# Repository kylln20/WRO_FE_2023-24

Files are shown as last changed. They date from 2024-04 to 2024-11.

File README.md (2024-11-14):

&nbsp;

🛠️ Engineering Documentation 🛠️
======

> This repository details Team Asparagus’ building and programming process in our second participating year of the 2024 WRO Future Engineers Competition.
&nbsp; 

---

## Content of Repository 
* `models` - 3D CAD files
* `others` - Other essential files
* `schemes` - Electrical schematics
* `src` - Main and other programs to run/control software
* `t-photos` - Team photos
* `v-photos` - Robot photos
* `video` - Video demonstration
&nbsp; 

Team Members
---

* Kayla Lin, 17, kylln2027@gmail.com
* Eric Rao, 16, ericrao08@gmail.com
* Brian Yin, 17, brianyin256@gmail.com

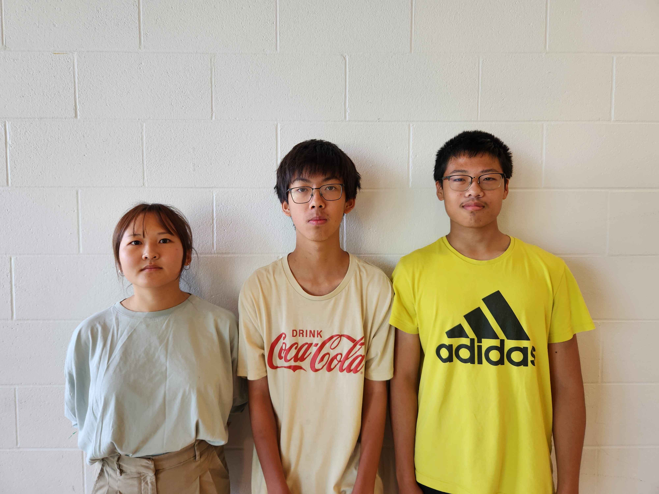
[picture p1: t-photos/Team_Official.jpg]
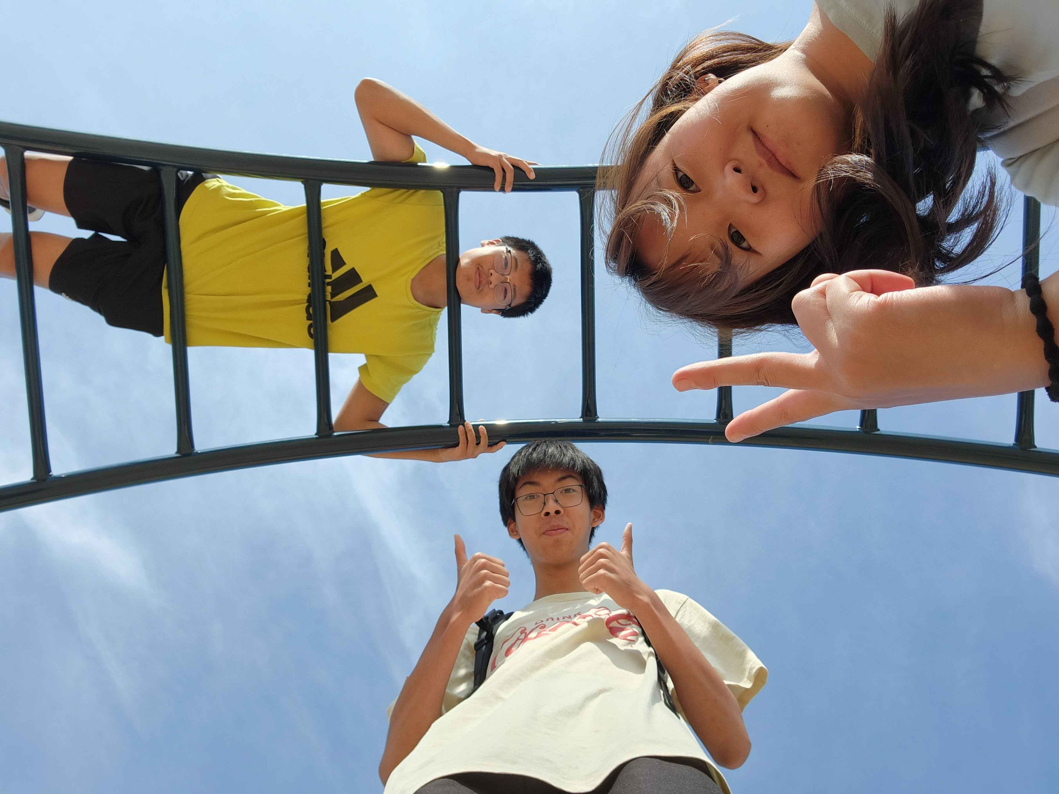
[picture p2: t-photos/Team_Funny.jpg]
 

***Kayla Lin (Left), Eric Rao (Middle), Brian Yin (Right)***

## 📖 Content of README 📖
* **[Hardware](#-hardware-)**
  * [Components](#%EF%B8%8F-components-%EF%B8%8F)
  * [Mobility Management](#-mobility-management-)
    * [Chassis](#chassis)
    * [Design](#design)
    * [Motors](#motors)
  * [Power and Sense Management](#-power-and-sense-management-)
    * [Power and Wiring](#power-and-wiring)
    * [Sensors](#sensors)
    * [Schematic](#schematic)
* **[Software](#-software-)**
  * [Initialization and Connection Process](#-initialization-and-connection-process-)
  * [Object Management](#object-management)
    *  [Object Detection](#object-detection--open-challenge--obstacle-challenge-)
    *  [Wall Detection/Management](#wall-detectionmanagement--open-challenge--obstacle-challenge-)
    *  [Signal Pillar Detection/Management](#signal-pillar-detectionmanagement--obstacle-challenge-)
    *  [Turning (Open Challenge)](#turning--open-challenge-)
    *  [Turning (Obstacle Challenge)](#turning--obstacle-challenge-)
    *  [Parking Lot Detection/Management](#parking-lot-detectionmanagement--obstacle-challenge-)
    *  [Three-Point Turn](#three-point-turn--obstacle-challenge-)
    *  [Backing Up](#backing-up--obstacle-challenge-)
    *  [Potential Improvement: Stuck Detection](#potential-improvement-stuck-detection--open-challenge--obstacle-challenge-)
* **[Assembly Instructions](#-complete-assembly-instructions-)**
  
&nbsp;

---

&nbsp;

🤖 Hardware 🤖
===

### ⚙️ Components ⚙️

| Name | Product | Price |
| --- | --- | --- |
| RC Car | [`Carisma GT24`](https://www.canadahobbies.ca/product/hobby-brands/carisma-rc/gt24-124th-4wd-toyota-celica-gt-four-st185-wrc/) | $263 |
| RC Car Battery | [`Gens Ace 1300mAh Battery`](https://www.adrenalinehobby.com/products/gens-ace-g-tech-1300mah-2s-7-4v-25c-lipo-deans-plug) | $35 | 
| Drive Motor & ESC | [`Furitek Komodo Motor + Lizard Pro ESC`](https://www.xtremerc.ca/products/furitek-scx24-stinger-brushless-power-system-w-1212-3450kv-brushless-motor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) | $226 |
| Turning Motor | [`Hitec HS-5055MG Servo Motor`](https://ca.robotshop.com/products/hs-5055mg-metal-gear-micro-servo-motor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) | $38 |
| Motor Mount | [`GT24 High Performance Alloy Motor Mount`](https://carisma-shop.com/products/gt24-alum-motor-mount) | $17 |
| CSI Camera | [`SainSmart Wide Angle Fish-Eye Camera`](https://www.amazon.ca/SainSmart-Fish-Eye-Camera-Raspberry-Arduino/dp/B00N1YJKFS/ref=sr_1_5) | $19 |
| Raspberry Pi HAT | [`HiWonder TurboPi HAT`](https://www.hiwonder.com/collections/raspberrypi-bionic-robot/products/turbopi?variant=40112905388119) | $61 [^1] |
| Raspberry Pi | [`Vemico Raspberry Pi 4`](https://www.amazon.ca/Vemico-Raspberry-Kit-Heatsinks-Screwdriver/dp/B09WXRCYL4/ref=sr_1_3) | $176 |
| Raspberry Pi Fan | [`GeeekPi Fan`](https://www.amazon.ca/dp/B07C9H9LJN?psc=1&ref=ppx_yo2ov_dt_b_product_details) | $19 |
| ON OFF Switch | [`DaierTek Switch`](https://a.co/d/05vnrpJD) | $13 |

**Total Car Cost: $867 CAD**

[^1]: This link is for the `Hiwonder TurboPi Car`, which uses the `HiWonder TurboPi HAT`. We contacted the manufacturer to purchase the HAT directly.

<sup>*3D printed parts were made with the [`BambuLab P1P`](https://ca.store.bambulab.com/products/p1p)</sup>

&nbsp;

🚗 Mobility Management 🚗
---

### Chassis
We use the chassis of the `Carisma GT24`, a pre-built 1/24 scale RC car (15 cm in length) to accommodate the added challenge of the magenta parking lot in the obstacle challenge. It allows us to park head-on, as opposed to parallel parking. Head-in parking has fewer steps, reducing our obstacle challenge time. Also, while head-in parking, the car only needs to be aware of what is beside it and what is in front of it, which can be assessed with a single front-facing camera. Comparatively, to perform parallel parking, a car will usually need to reverse, requiring an additional rear-facing sensor. Such would unnecessarily complicate the system.

The chassis also enables a four-wheel drive system, with pre-integrated gearboxes. This system offers benefits over a two-wheel drive system increasing the car's traction, stability, and acceleration due to the power distribution between four wheels instead of two. 

#### Potential Chassis Improvement
Although the chassis has many benefits, its design only allows a maximum turning angle of 50 degrees. Although sufficient for our task, a car with a chassis with a greater turning angle would more easily navigate the challenges and could be pushed to navigate at a higher speed. Swapping the chassis for one with a higher turning angle, whether store-bought or 3D-printed, would significantly improve the car's movement and obstacle avoidance. We have also seen that one can modify the original chassis to have a much greater turning angle, but we decided against it due to time constraints. 

This is a video example of a modification done to a similar chassis: 

[K989 Modification](https://www.youtube.com/watch?v=JmsCxSgEJnU)

### Design 

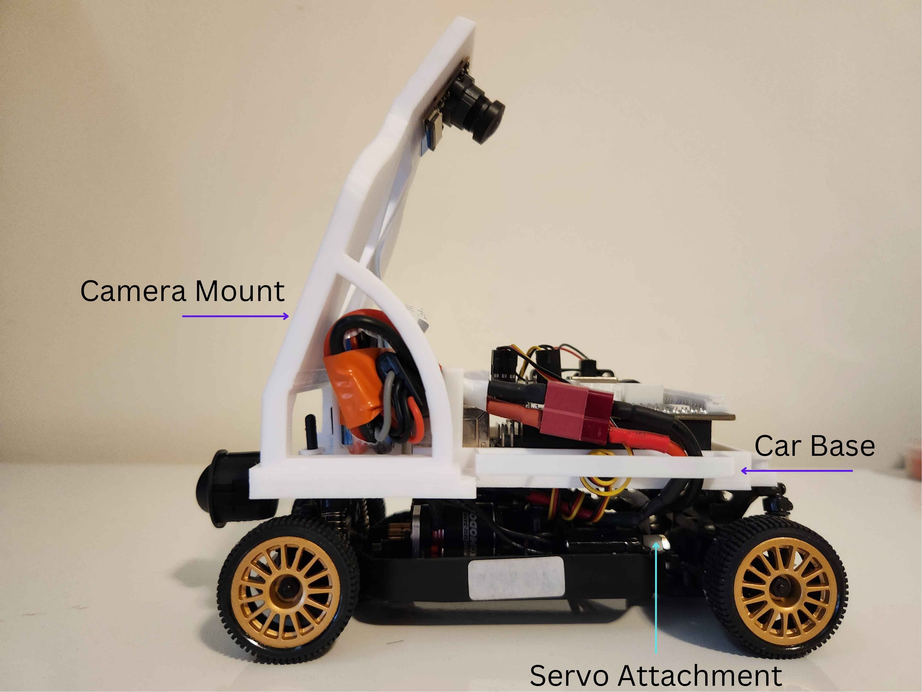
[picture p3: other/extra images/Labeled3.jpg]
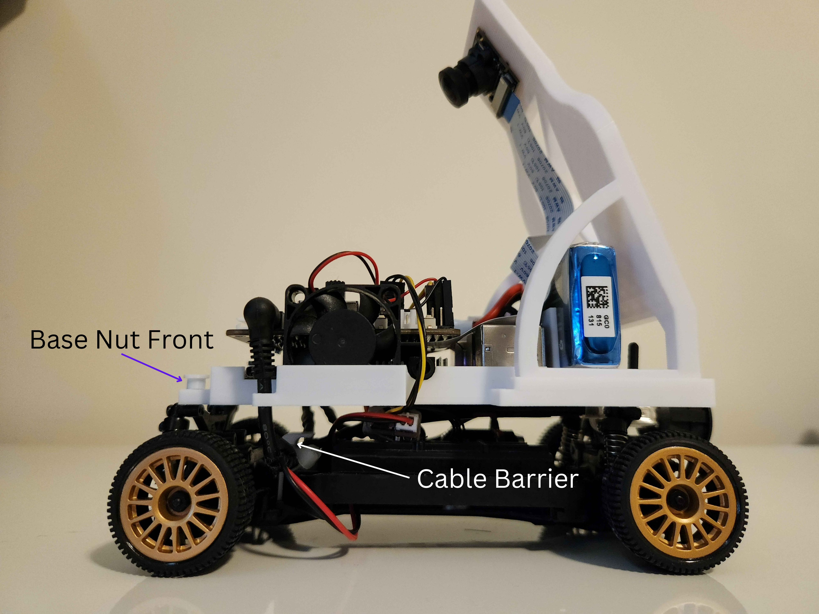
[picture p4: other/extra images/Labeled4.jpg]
 

1. **Base Nut Front / Back**: used to secure the 3D-printed base onto the chassis
2. **Cable Barrier**: is attached to the chassis to prevent cables from interfering with tires
4. **Camera Mount**: the piece the camera is attached to, adds height and tilt
6. **Car Base**: the main platform of the car, is attached to the chassis through 4 posts, components of the base include:
    - Holder for Raspberry Pi
    - Holder for cooling fan 
    - Holder for battery
    - Vertical post to route battery cable
    - Cable ladder organizer on the right side
    - Hook on the left to hold the power cable in place
7. **Servo Attachment**: attaches to the servo motor and controls steering

The design of the camera mount changed from our national competition with it becoming one singular piece mounted directly on the printed car base. 

It used to be three seperate pieces, mounted to thin plastic posts on the chassis. 

This redesign allowed for a much more sturdy camera mount ensuring the camera is stable during object detection. 

### Motors
Our car uses a `Furitek Micro Komodo Brushless Motor`. Brushless motors refer to the lack of small "brushes" in the motor that a brushed motor would have. This design reduces motor friction, improving lifespan, torque, efficiency, and acceleration. Adequate torque is essential during slow turns to avoid cogging.

The `Furitek Micro Komodo Brushless Motor` is also very small compared to other RC car motors, making it fit well with our small chassis. It fits conveniently in the place of the original motor, with a metal gearhead that connects to the rest of the drive system. Despite its size, the motor is remarkably powerful. With a KV (RPM/Motor) of 3450, this motor allows us to reach high speeds without maxing out the motor. 

The Motor is mounted on an aluminum motor mount for increased durability and passive cooling. 

The motor receives power and signal via PWM from the `Furitek Lizard Pro Electronic Speed Controller (ESC)`. This ESC provides constant regulation that ensures we can maintain a constant pace, with smooth acceleration and deceleration.

To control steering we use a `Hitec HS-5055MG Servo Motor`, a three-wire connection (signal, voltage, ground) metal gear servo motor. We control and power it from the `Raspberry Pi Hardware Attached on Top (HAT)`. The original 5-wire servo that came with the RC chassis had a weaker plastic gear and was non-programmable due to being connected to a customized circuit board. Due to both those flaws, we replaced the original servo. 

The servo is connected to the front wheel axis with a 3D-printed adapter piece that is screwed onto the servo shaft. It has a torque of about 1.5kg/cm at 6V allowing it to quickly and precisely change the direction of our car. This precision is vital for our needs in the obstacle challenge and open challenge.

&nbsp;

⚡ Power and Sense Management ⚡
---

### Power and Wiring
Our car gets power from a single `Gens Ace 1300mAh 7.4V Battery`. This battery was chosen mainly due to its high 45 C rating allowing for a higher discharge of electricity while still being lightweight and compact. This powerful battery easily satisfies the power demands of the Raspberry Pi, camera, 7.4V DC motor, and servo motor. Although the `Raspberry Pi 4B` runs off 5V, our Pi HAT contains a voltage regulator allowing the 7.4V output of the battery to be limited to 5V to power the Raspberry Pi. 

The wires of the battery are soldered to the circuits of the Raspberry Pi and ESC in parallel with a switch controlling the passage of electricity at the beginning of the circuit. This design eliminated the need for two separate batteries, saving space, simplifying our circuit, and reducing the car’s overall weight.

#### Potential Circuitry Improvements
Our switch is large and the wires connecting to it are too long. It extends the length of our car by a couple of centimeters, and its exposed nature is a structural weak point of the car. Our design could be improved by using a smaller switch with a shorter length of wire, making the car more compact. 

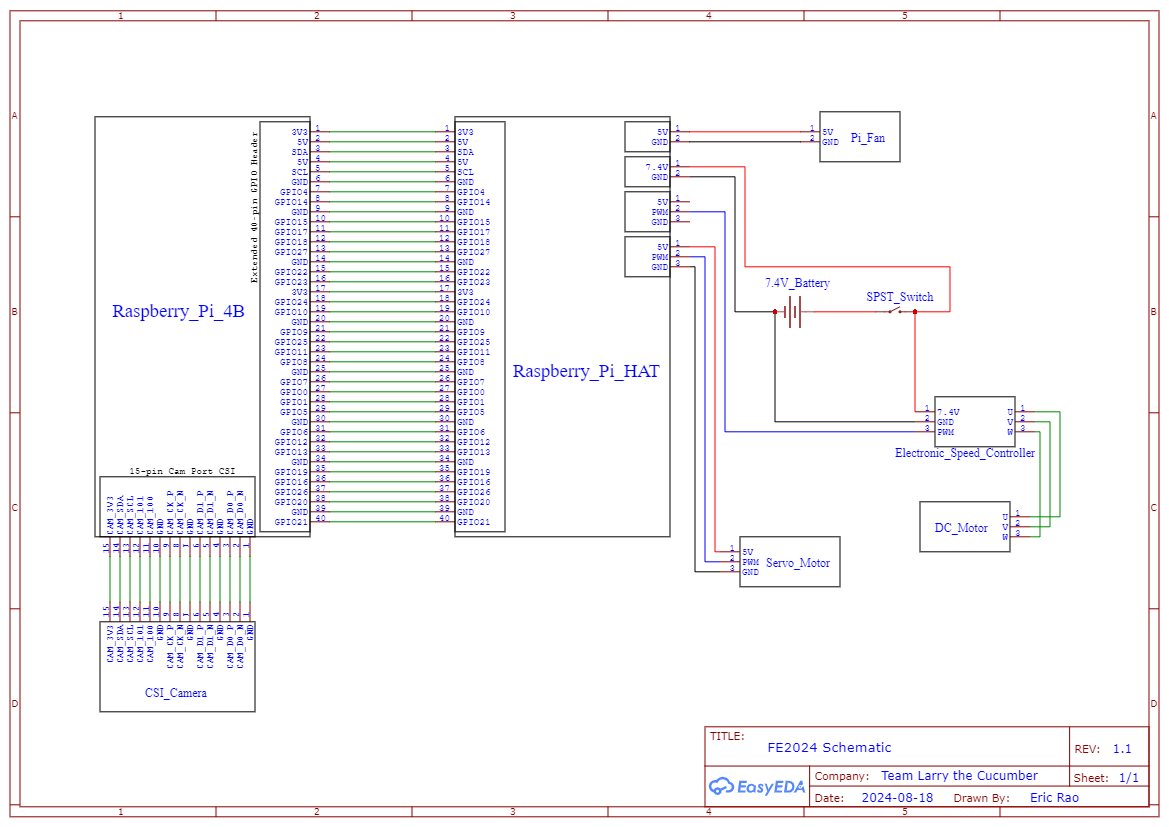
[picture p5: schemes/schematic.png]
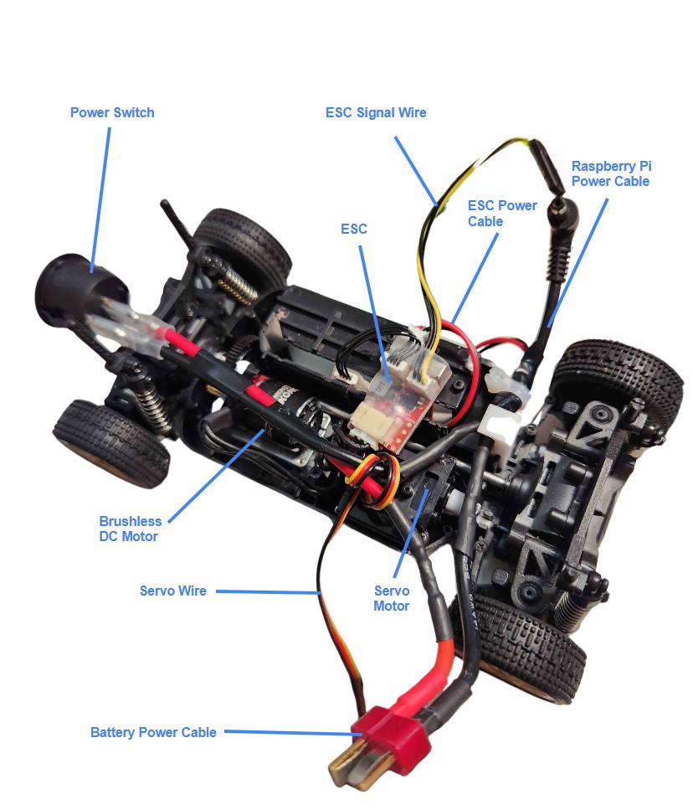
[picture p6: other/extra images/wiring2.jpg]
  

### Sensors

For our sensors, we only use one camera to navigate both challenges. This was chosen over using LIDAR or adding ultrasonic sensors, as this helps to keep our power consumption as low as possible, keep our car and software design as simple as possible, and avoid more possible failure points. 

We use a `SainSmart Wide-Angle Camera`, which carries pixel data to the Raspberry Pi via a Camera Serial Interface (CSI) cable. We chose a CSI camera over a USB camera due to its low latency, high performance, low power consumption, and smaller size. Unlike a USB camera, the CSI camera has the drawback of not being hot-swappable, but overall, the benefits outweigh the cost.  The 'SainSmart Camera' also has a fish-eye lens which enables it to have a field of vision angle of 160 degrees, which allows us to detect more of the game field- whether that be the signal pillars, the coloured lines on the mat, or the walls- both at the front and to the sides of the car. The greater quantity of information allows the program to more accurately plan the car's movements.

Based on said pixel data, we can identify objects based on their size and colour. From such information, our program will calculate the desired speed and turning angle which it will send through the HAT to the DC and servo motors respectively with pulse-width modulation (PWM) signals. 

The camera uses a 5 MP OV5647 Sensor, which is adequate to detect basic colours for our needs, but has its limitations in different lighting conditions and distinguishing between similar colours

For the Canadian National WRO Future Engineers competition, the camera's sensitivity to different lighting conditions made it difficult to consistently run code that is unaffected by the environment and direction. Improvements we considered were changing the camera settings or attaching a lamp to the car to ensure consistent lighting. However, a solution was found by processing the colours using a different system (detailed in the Software section).

#### Potential Sensing Improvements
Although this system is sufficient for our needs, object detection can be further improved by using a camera with a higher-quality sensor such as the [Raspberry Pi HQ Camera M12](https://www.pishop.ca/product/raspberry-pi-hq-camera-m12/), which performs better in different lighting and can easily distinguish between colours. An improvement to the camera would help maintain consistency in the programs to an even higher degree.

Another possible improvement is the implementation of a `Gyro Sensor`, which tracks the car's orientation. We attempted to use a [BerryIMU](https://ozzmaker.com/product/berryimu-accelerometer-gyroscope-magnetometer-barometricaltitude-sensor/) for this function but decided against using it due to the extra complexity it added and its inconsistent readings. By tracking the car's orientation and keeping it heading at the same angle, it is possible to make parking more consistent and allow the car to control more precisely allowing it to go faster for the open challenge. 

An example of an alternative gyro sensor that may offer higher accuracy is the [BNO055 Absolute Orientation Sensor](https://www.pishop.ca/product/adafruit-9-dof-absolute-orientation-imu-fusion-breakout-bno055/)

&nbsp;

💻 Software 💻
===
We use a `Raspberry Pi 4 Board` as our single board computer (SBC). It is connected to the HAT, from which it takes and processes sensor input to return turning-angle and speed values back to the HAT, which then gets sent to the servo and DC motors respectively. 

The program running on the Raspberry Pi is written in Python.     

🛜 Initialization and Connection Process 🛜
---
We used the Raspberry Pi imager to write the Raspberry Pi operating system onto an SD card that allowed us to use our Pi HAT. Once the operating system is downloaded onto the SD card, when the Raspberry Pi is running AP (Access Point) mode, we can connect to the Raspberry Pi through wifi. Once we have selected the Access Point in the wifi tab, we use VNC Viewer to connect remotely to and interact with the Raspberry Pi using a set IP address. 

Object Management
---

### Object Detection <sub> (Open Challenge / Obstacle Challenge) </sub>

The camera captures an image, which the program then converts from OpenCV’s default pixel data format of BGR (blue, green, red) to `LAB (lightness, green-red, blue-yellow)`. We chose to use the LAB colour space because it performs better no matter the lighting environment. Previously, we used `HSV (hue, saturation, value)`. It was easier to select ranges for our colour masks than BGR or RGB. While LAB makes it less intuitive to find the colour ranges, the colour masks themselves are better for detecting the objects, as the two values concerning colour allow for better control than the H variable in HSV does. A significant improvement from the change is that the colour masks defined using LAB values have eliminated instances where the robot mistakes the magenta parking lot for being a red signal pillar.
```py
img_lab = cv2.cvtColor(img, cv2.COLOR_BGR2Lab)
```

Then, we perform a Gaussian blur on the image using the OpenCV library `GaussianBlur()` function. This smooths any edges in the image and removes small noise, making the overall shape of any obstacles easier to detect. 
```py
img_blur = cv2.GaussianBlur(img_lab, (7, 7), 0)
```
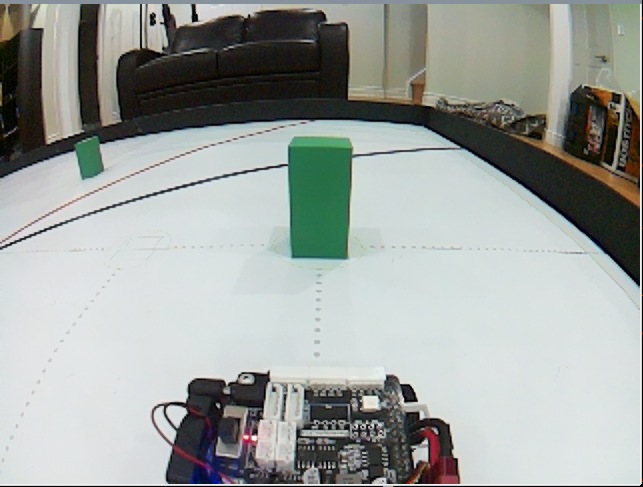
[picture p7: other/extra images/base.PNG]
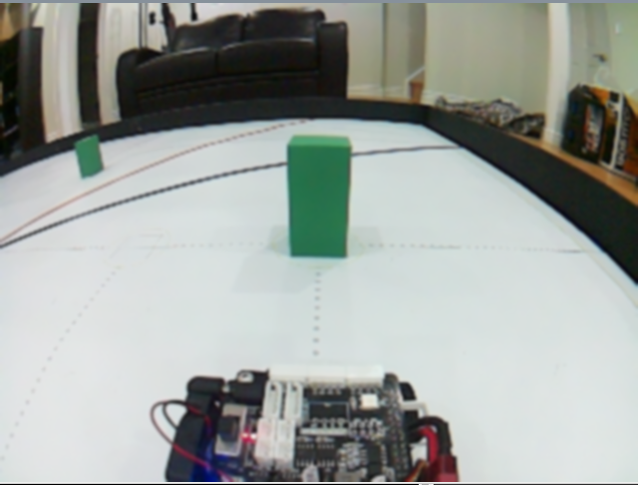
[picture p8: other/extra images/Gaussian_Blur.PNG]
 

Then, `LAB thresholding` is applied, which checks if all pixels are within a certain LAB range. The resulting image has pixels within this range (areas of interest) as white, and everything else black. This is done with the OpenCV library `inRange()` function, where we specify the input image and a colour mask (range of LAB values).

```py
#LAB colour masks for all ranges, the first array represents the lower bound, and the second represents the higher bound
rMagenta = [[0, 171, 106], [255, 195, 135]]
rGreen = [[0, 45, 0], [255, 117, 153]]
rBlue = [[54, 124, 25], [148, 164, 121]]
rOrange = [[0, 163, 163], [255, 191, 204]]
rBlack = [[0, 109, 113], [59, 137, 150]]
```

The colour mask[^3] allows us to account for how lighting causes colour variation for the target object. Additionally, the input image can be modified with array splicing so we only search in a specific region of interest. By only searching in the region of interest, we also reduce the processing required for the car to produce a speed and angle value to send to the motors. This gives the robot time to analyze more images, which means more frequent decisions, and obstacles that can be avoided more efficiently. This improvement made after nationals and led to the car avoiding obstacles better. 

```py
img_segmented = img_lab[ROI[1]:ROI[3], ROI[0]:ROI[2]]

mask = cv2.inRange(img_segmented, lower_mask, upper_mask)
```

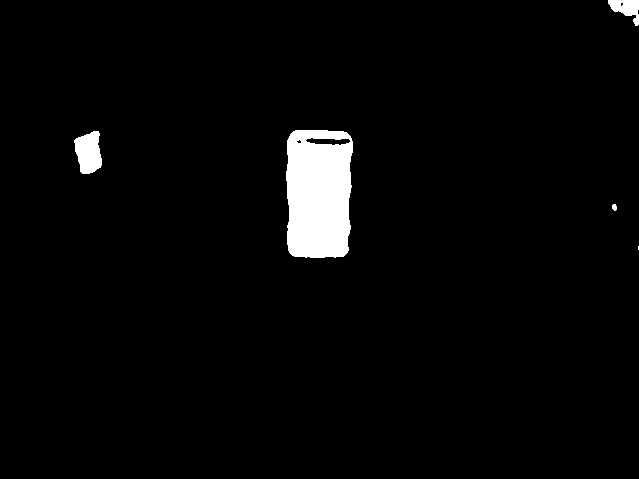
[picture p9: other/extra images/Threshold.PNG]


Following the creation of a mask, we perform two other operations on it: 

- Erosion: this morphological operation finds and removes areas of noise in the binary (black and white) image
```py
cv2.erode(mask, kernel, iterations=1)
```
- Dilation: this morphological operation fills in any gaps in bright areas in the binary image
```py
cv2.dilate(mask, kernel, iterations=1)
```
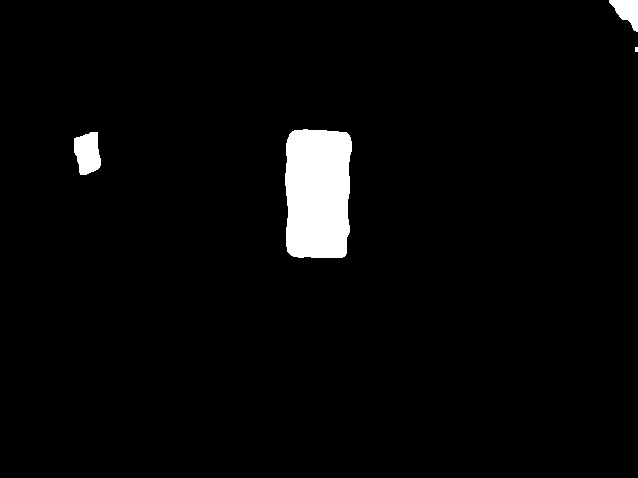
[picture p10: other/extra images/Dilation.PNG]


These operations ensure only pillars are detected and their shape is accurate. 

The bounded white areas can then be extracted as a list of contours within a specified region of interest.

```py
contours = cv2.findContours(mask, cv2.RETR_EXTERNAL,
    cv2.CHAIN_APPROX_SIMPLE)[-2]
```

We use this method of detection for all target objects including the signal pillars, the coloured lines on the game mat, the magenta parking lot, and the black walls around the track. This processing is placed in a function that takes in the LAB image, LAB mask ranges, and the ROI in which contours should be detected. The function returns a list of contours from the thresholded mask: 

```py
def find_contours(img_lab, lab_range, ROI):
```
In a separate function: 

```py
def max_contour(contours, ROI):
```

we measure the area of the specific contour using the OpenCV library function contourArea().

```py
area = cv2.contourArea(cnt)
```

The area is returned in an array with additional data as the x-coordinate, y-coordinate, and the contour object. 

#### Potential Object Detection Improvements

This algorithm is not perfect and the contour will not be perfectly aligned with the shape of the pillar, but it is sufficient for our needs. The accuracy of the object detection algorithm could hypothetically be improved with the use of even more morphological operations performed over more iterations. 

One approach we tried was to use a bilateral filtering algorithm to better retain the edges of the pillars,

```py
 cv2.bilateralFilter(image, d=9, sigmaColor=75, sigmaSpace=75)
```

but the program slowed from 30 fps down to 8 fps. If one could optimize the Raspberry Pi 4's performance or make our obstacle challenge code more efficient, these operations could be performed easily leading to more accurate object detection. 

[^3]: The colour masks used for each object still depend on the environment the car is in. We had difficulties getting the program to perform well in a room with yellow-tinted lights instead of white LEDs, especially before switching to LAB. This required changing the colour masks when running the car in that environment. An existing code that was useful for finding/adjusting colour masks was from an [OpenCV tutorial](https://docs.opencv.org/3.4/da/d97/tutorial_threshold_inRange.html), which was modified to be the ColourTesterLAB.py code.

### Wall Detection/Management <sub> (Open Challenge / Obstacle Challenge) </sub>

The wall contours are detected with one region of interest for each wall. 

The areas of each contour are added to their respective variable, leftArea for the area of the left wall and rightArea for the area of the right wall. 

In addition to the area of the black wall, we also add the areas of any magenta contour we see to help avoid collision with the parking lot. 

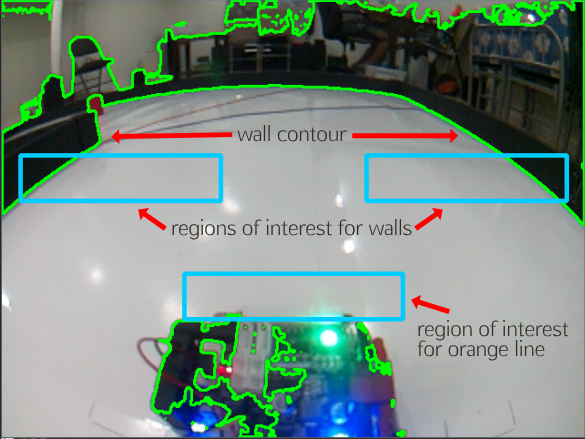
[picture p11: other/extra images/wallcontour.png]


To stay centered when driving straight, we use a proportional derivative (PD) algorithm, which involves calculating the difference between the areas of the two contours and calculating a turning angle based on:

* A difference in contour areas (`error`)
* A straight constant (`straightConst`)- the number that would be sent for the car to go straight
* A proportional constant (`cKp`) - the constant that gets multiplied by `error` 
* A derivative constant (`cKd`) - the constant that gets multiplied by the difference in the error and the previous error (`prevError`)

The resulting calculation is:
```py
 angle = int(straightConst + error * cKp + (error - prevError) * cKd)
```
&nbsp;

### Signal Pillar Detection/Management <sub> (Obstacle Challenge) </sub>

In the Obstacle Challenge, if a signal pillar is detected, the program will switch from calculating the angle based on the walls to the signal pillar instead. 

Signal pillars are found with green and red colour masks, and by searching in a region of interest specific to the locations of the obstacles. 

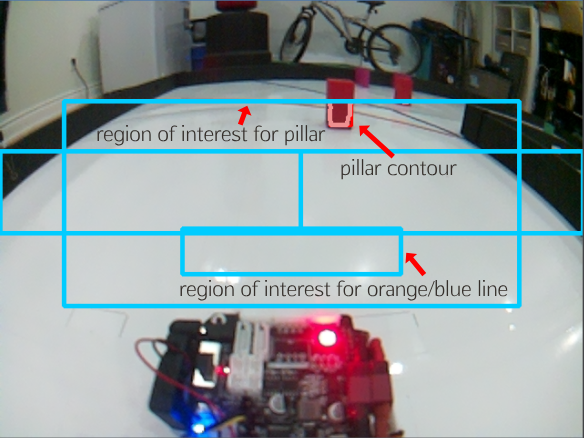
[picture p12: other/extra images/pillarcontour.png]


A function called `boundingRect()` approximates a rectangle around the selected contour. `boundingRect()` also returns the x and y coordinates of the rectangle’s top left corner. When applied to the contour of the signal pillar, this can be used to determine its location.

Then, a PD calculation is applied based on the difference between the x-coordinate of the pillar, and the target x-coordinate. The target x-coordinate for the green pillars is near the right side, as the car needs to pass it on the left side. The opposite is true for the red pillars. The calculation also includes a value changing the angle based on how close the pillar is by using the pillar's y-value. 

```py
#calculate error based on the difference between the target x coordinate and the pillar's current x coordinate
error = target x - current x

#calculate new angle using PD steering
angle = int(straightConst + error * cKp + (error - prevError) * cKd)

#adjust the angle further based on the y-coordinate (cy) value
angle -= int(cy * y) if error <= 0 else -int(cy * y)
```

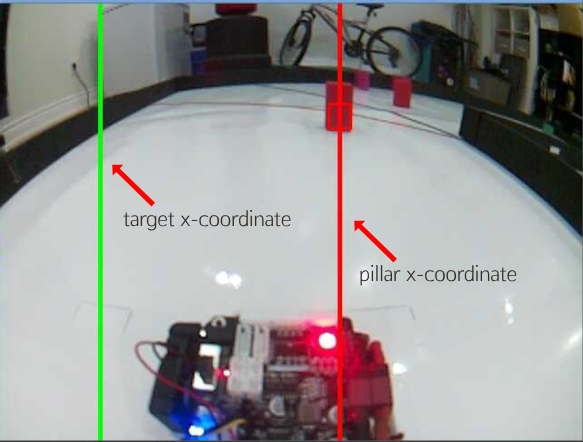
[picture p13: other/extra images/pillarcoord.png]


In the event there are 2 or more pillars seen, we determine which one to focus on by calculating the distance between the bottom-middle of the screen to the bottom-middle of the pillar. We use the closest pillar to calculate the servo angle. 

Additionally, we change the control variables to be weaker when 2 or more pillars of the same colour are seen, so the car can successfully navigate tight corner cases. 

While we detect a pillar, if the area of the left or right walls becomes too large, we deselect the current pillar so the wall areas determine the angle instead. This allows the car to turn towards the middle and avoid hitting the wall

After twelve turns, once the car has completed three laps and is searching for the parking lot, the target x-coordinate is such that the car drives toward the outside of the red and green pillars.

&nbsp;

### Turning <sub> (Open Challenge) </sub>
The car begins a turn when the area of either wall is below a certain threshold. It then turns in the direction of the wall with the lesser area.

```py
if leftArea <= turnThresh and not rTurn:
    lTurn = True

elif rightArea <= turnThresh and not lTurn:
    rTurn = True
```

During a turn, we set the servo to a default turning angle of 25 degrees (sharp left/right). However, if the angle calculated through the difference of wall areas is greater than 25 degrees and is below the absolute angle limit (max left/right), the car will use this angle instead of the default 25 degrees. This ensures we don’t hit the wall during tighter turns. 

```py
if lTurn:
    angle = min(max(angle, sharpLeft), maxLeft)
elif rTurn: 
    angle = max(min(angle, sharpRight), maxRight)
```

 The turning ends once the area of the side that was below the threshold regains enough area. Additionally, to count the number of corners the car has passed, the program tracks whether the orange or blue lines on the mat have been detected. The line is searched for using our object detection algorithm, with an orange colour mask on a centered region of interest. Once the area of the line contour has passed a certain value, the program knows the car has passed a corner.
 
```py
if (rightArea > exitThresh and rTurn) or (leftArea > exitThresh and lTurn): 
    end turn
    increase number of turns if orange or blue line was detected
```
&nbsp;

### Turning <sub> (Obstacle Challenge) </sub>
Unlike the open challenge, in the obstacle challenge, we can't detect turns by the areas of walls due to the need to avoid pillars at the entrance and exit of the turn. To compensate, the obstacle challenge code instead enters a turning mode once the nearest mat line (blue if travelling clockwise, orange if travelling counter-clockwise) has been detected and is of a certain area. 

The car is automatically set to the maximum 50-degree turning angle to ensure it can see pillars quickly after a turn. 

If it detects a signal pillar, the turn ends immediately, and the angle calculation is based on the signal pillar. Otherwise, like in the open challenge, the program will exit the turning mode when the difference between the two wall contours has decreased to a certain threshold, and the angle calculation will be based on the wall area difference.

If a pillar is detected during a turn, we found the car may struggle in certain cases to successfully turn around the pillar when the angle of approach is very narrow. To counteract this, we added a 5th region of interest for detecting the wall in front to turn earlier. If a turn is ended by seeing a pillar, we check if this region of interest is filled and turn to the maximum angle in the same direction as the car's turning direction even if we still detect the pillar. 

If the pillar's area becomes too large while turning, the car turns too early and is on course to hit. In this case, we straightened the car's turning angle until the area was lower than a certain threshold to avoid collision. 

```py
if ((ROI5_area > threshold and turnDir == left) or (ROI5_area > threshold and turnDir == right)):

    if pillar_area > threshold:
        turn_angle = straight
    else: 
        if turnDir == right:
            turn_angle = sharp_right
        else:
            turn_angle = sharp_left
```
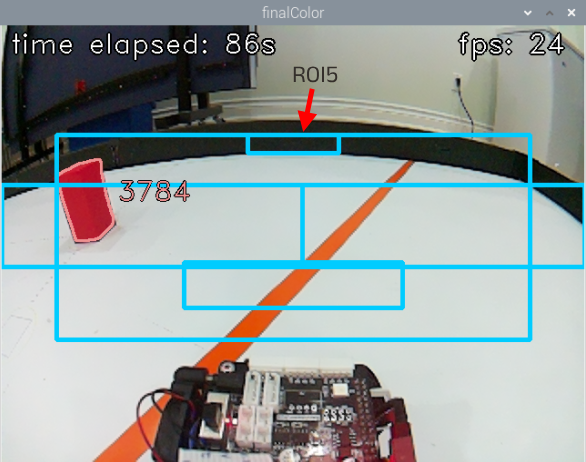
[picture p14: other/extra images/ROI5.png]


As we don't want this region of interest to interfere with our regular driving algorithms, the region of interest is only present when needed in tight cases where the area of the left wall area is large enough when starting a left turn or the right wall area is large enough when starting a right turn. 

```py
if (turnDir == right and orange_line_detected) or (turnDir == left and blue_line_detected): 
    if pillar_area > 0 and ((left_wall_area > threshold and turnDir == left) or (right_wall_area > threshold and turnDir == right)):
        show ROI5 and use it
```
            
The region of interest is then hidden once the camera no longer detects the wall in front, a pillar in front, or there is a large enough difference in the wall areas. 

```py
if (pillar_area == 0 and ROI5_area > threshold) or (wall_area_difference > threshold and ROI5_area > threshold):
     hide ROI5
```

This approach makes the car turn earlier making the turns around pillars much more consistent, allowing our car to control better at faster speeds. 

&nbsp;

### Parking Lot Detection/Management <sub> (Obstacle Challenge) </sub>
After three laps are completed, we set a timer of two seconds so we stop in the starting section, the car then moves to pass all pillars on the outside to make it easier for the car to park. 

During parking, ROI5 is always shown to make sure turns are as sharp and quick as possible for an easier approach while parking. 

The parking walls are found with magenta colour masks and by searching in two regions of interest that were used to detect walls, again with LAB thresholding. This starts after twelve turns. Any time after thirteen turns, parking mode will start after a magenta contour of the right size reaches a specific Y-coordinate in either of the regions of interest.

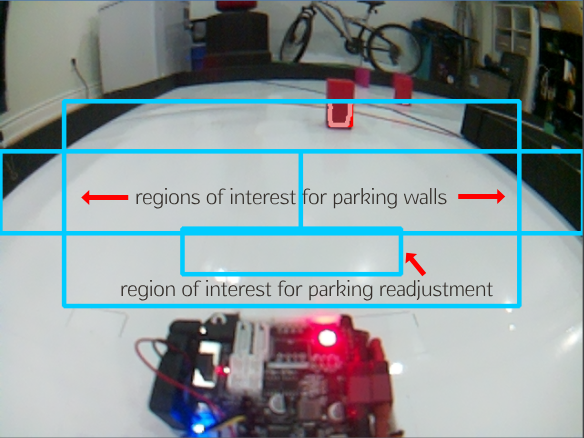
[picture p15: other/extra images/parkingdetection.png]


Once the magenta parking lot has been found in the left or right region of interest, we delay using time.sleep() based on the detected area to ensure the car doesn't turn too early. 

```py
time.sleep((lot_area) / (constant))
```

After, the car turns to the direction in which the parking lot has been detected. If the program detects a magenta contour in the central region of interest, the car is not centered between the parking walls. To avoid hitting the walls, the car backs up to allow more distance to adjust. Additionally, while parking into the lot on the left, if the right region of interest is found to have a large enough area in both magenta and black, the car is too far left, meaning we have to turn right.
```py

if parking lot is on the right:
     
     if parking lot detected in front:
         back up while turning left
     else:
         turn right
 
 elif parking lot is on the left:
     
     if right wall area > threshold and right parking lot area > threshold:
         turn right
     if parking lot detected in front:
         back up while turning right
     else:
         turn left

if the area of the wall in front > threshold:
    turn the wheels straight and stop the car
```

The car stops once the area of the wall detected in the middle is large enough, using the same region of interest (ROI) that detects the orange/blue lines.

&nbsp;

### Three-Point Turn <sub> (Obstacle Challenge) </sub>

After the eighth turn has been counted by seeing a wall or a pillar, we check whether a three-point turn is required. This is done by checking whether there was a pillar directly in front of the car at the start of the program and the area of the pillar detected during the 8th turn. 

We determine if there was a pillar in front of the car in the starting section by seeing if the maximum pillar area we detected before the first turn is larger than a certain threshold or if two pillars of a single colour were detected before the first turn. 

```py
if orange line detected and turn direction == right or blue line detected and turn direction == left
  if turns == 0 and pillarAtStart == not set:
     if largest pillar area > threshold:
         pillarAtStart = True
     else:
         pillarAtStart = False

if num_pillars_g >= 2 or num_pillars_r >= 2 and pillarAtStart == not set:
    pillarAtStart = True
```

If there was no pillar directly in front of the car in the starting section, we can assume that any pillar seen during the 8th turn is the last pillar of the second lap. 

If a pillar was directly in front of the car (in the starting section), we know it could not be the last pillar of the second lap. If there is another pillar in the starting section, it would be considered the last pillar in the second lap. If this extra pillar is present, it would be close to the edge as it's impossible to have a pillar in the middle with two pillars. This means that the area of the pillar that is seen during the turn must be large. Therefore, we check if the area of the pillar is above a threshold. 

If no pillar is detected during the 8th turn, the last pillar detected is the last pillar of the second lap so we use it to determine whether to do a three-point turn. 

```py
if turn is ended by seeing the wall: 
     if last pillar seen is red: 
          perform three-point turn
          
if turn is ended by seeing the pillar: 
     if there was a pillar directly in front: 
          if area of current pillar is larger than a threshold and is red: 
                 perform three-point turn
     if there was no pillar directly in front and current pillar is red: 
          perform three-point turn
```

This approach to determining the need to perform a three-point turn proved much more consistent than our last approach, which relied heavily on specific wall area and pillar area thresholds vulnerable to lighting and colour. 

Once we know a three-point turn must be performed, the car will immediately turn to the left unless it detects a red pillar, in which case it will turn after passing the red pillar by waiting until no pillar is detected or the area of the wall in which the car is turning towards is large enough. The car will turn left until it detects the wall or parking lot in front using the same ROI used for detecting the coloured lines. It will then back up while turning to the right for a certain period. Then the program will resume.

After the initial three-point turn, if the car detects a large black area in front again, the initial three-point turn isn't sharp enough, so another three-point turn is performed.

If the car doesn't detect the wall in front and instead comes too close to a pillar, it means the car has already turned around, so we count an extra turn.

### Backing Up <sub> (Obstacle Challenge) </sub>

In certain cases where the car may not be able to pass a pillar without moving it, the car will move back. We determine when the car will move back by checking the area of the current selected pillar and its distance from its target x-coordinate

```py
if pillar area > threshold and current x-coordinate is far from its target x-coordinate:
    move back 
```

### Potential Improvement: Stuck Detection <sub> (Open Challenge / Obstacle Challenge) </sub>

In our testing, very rarely our car would get stuck on the wall and not be able to move. Although this happens such a small percentage of the time, having a method to counteract this would be good to have. 

One method we considered to check for when we were stuck was comparing the camera image changes and seeing if they were similar. We decided against its implementation due to the rarity of becoming stuck and our time constraints. 

This could be implemented with two methods: 

1. Mean Squared Area (MSE): measures the average squared difference between the pixel values of the two images.
2. Structural Similarity Index (SSIM): a scikit-image method that offers a more accurate comparison at the cost of speed.

To use SSIM download the scikit-image library through the Raspberry Pi terminal: 

```py
sudo pip install scikit-image
```

Here's an implementation of both methods: 

```py
import cv2
from skimage.metrics import structural_similarity as ssim
import numpy as np

def mse(image1, image2):
    # Compute the Mean Squared Error between the two images
    err = np.sum((image1.astype("float") - image2.astype("float")) ** 2)
    err /= float(image1.shape[0] * image1.shape[1])
    return err

# Load the two input images
imageA = cv2.imread('path/to/first/image.jpg')
imageB = cv2.imread('path/to/second/image.jpg')

# Convert the images to grayscale
grayA = cv2.cvtColor(imageA, cv2.COLOR_BGR2GRAY)
grayB = cv2.cvtColor(imageB, cv2.COLOR_BGR2GRAY)

# Calculate MSE and SSIM
m = mse(grayA, grayB)
s, diff = ssim(grayA, grayB, full=True)

# Print the results
print(f"MSE: {m}")
print(f"SSIM: {s}")
```

To ensure these stuck detection methods don't interfere with the regular Obstacle Challenge algorithm, we can make it run in parallel using multi-threading. 

Implementation with the Python threading library: 

```py
import threading

def stuck_detect():
    while True:
        #implement stuck detection here

# Create a new thread
thread1 = threading.Thread(target=stuck_detect)

# Start the new thread
thread1.start()

#continue with obstacle challenge program
```

&nbsp;

🔨 Complete Assembly Instructions 🔨
===

1. **Strip the `Carisma GT24` chassis.**
   - The car itself comes with a realistic car cover. This is purely cosmetic and can be removed, along with the mounts supporting it.
   - The electrical components are housed within the center of the chassis. They can be accessed by unscrewing another plastic cover
     
2. **Removing unnecessary parts**
   - Take out the DC motor, servo motor, ESC, and RC module. The first three parts listed will be replaced by higher quality components.
   - This will require unscrewing as well as ripping parts off of the adhesive
   - Note that some rear portions of the car will need to the disassembled temporarily to access some screws

3. **Install the new parts**
   DC Motor Installation:
   - Install the `Aluminum DC Motor Mount`
   - Install The `Furitek Micro Komodo Brushless Motor` onto the motor mount
   - The motor gear may need to be replaced. Judge this based on how well it meshes with the drive system gears
   Servo Motor Installation: 
   - 3D-print our servo attachment, place it on the head of the servo motor, and secure it with a screw and nut. 
   - The `Hitec HS-5055MG Servo Motor` also needs its wings clipped before installing

5. **Wiring**
   - Ensure everything is wired properly, according to the schematic above.
   - Here, you can also splice your switch into your battery wires
   - Although they haven't been installed yet, you can test the connection to the Raspberry Pi and the battery
   - Although the Raspberry Pi and ESC both contain switches, we only use our self-added switch to turn on the whole system
   - 3D print a `cable barrier` and attach it onto the chassis to prevent cables from interfering with steering

6. **3D Printed Parts**
   - Print a base and a camera mount. Our designs can be found in this repository.
   - Note that our base was designed to fit smoothly on top of the chassis with the holes matching the 4 posts of the chassis
   - The camera screws onto the camera mount at the top where 4 small holes are present
   - The camera mount attaches by inserting it into the rectangular slots on the rear of the car base
   - These new parts provide housing for the camera, Raspberry Pi, Raspberry Pi Fan, and battery
   - The Raspberry Pi HAT fits nicely on top of the Raspberry Pi, secured and connected through the GPI0 pins

9. **Configuration**
   - Download the [Raspberry Pi Imager](https://www.raspberrypi.com/software/)
   - With the imager, prepare your MicroSD card and copy the [TurboPi OS](https://drive.google.com/file/d/1sBCMegKXQaT8nuhjBM0KjXP2YUlaAOju/view). Then, insert the card back into the Pi
   - Power on your Raspberry Pi. By default it is running in Access Point (AP) mode meaning you have to connect via a Wifi Access Point.
      - Search for a Wifi connection with the format: `HW-xxxxxx`
      - It will have a password of `"hiwonder"`
   - Remotely access your Raspberry Pi through [VNC Viewer](https://www.realvnc.com/en/connect/download/viewer/) by entering the IP address `192.168.149.1`
   - VNC Viewer will ask for a username + password
      - Username: `"pi"`
      - Password: `"raspberry"`
   - Now you can access your Raspberry Pi

10. **Load source files**
   - Go to the folder: /home/pi/TurboPi/HiwonderSDK and add the files found in `src`
   - For this competition, you also need to `auto-run` your program
   - Open the Pi terminal and run `sudo nano /etc/rc.local`
   - Add the program `(ObstacleChallengeV2.py/OpenChallenge.py)` with `sudo bash -c 'sudo python3 /home/pi/<<directory>>/<<filename.py>>' &`, before the line `exit 0`
   - Save and reboot
   - On start-up, the file placed in the rc.local file will run automatically
     
9. **Congratulations! You've built our robot!**
    - You can try running the `src` files directly from the Pi terminal using sudo python3 <<filename.py>> while in the right directory to run our program
    - You can use `Thonny`, a pre-installed compiler on the Raspberry Pi, as a code editor for the programs
    - Any other information can be found on this repository
    - Thanks for reading!

&nbsp;

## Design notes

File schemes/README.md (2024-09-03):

Electromechanical diagrams
====

This directory contains a schematic diagram made in EasyEDA, that illustrates all the electromechanical components of our car, and how they connect.

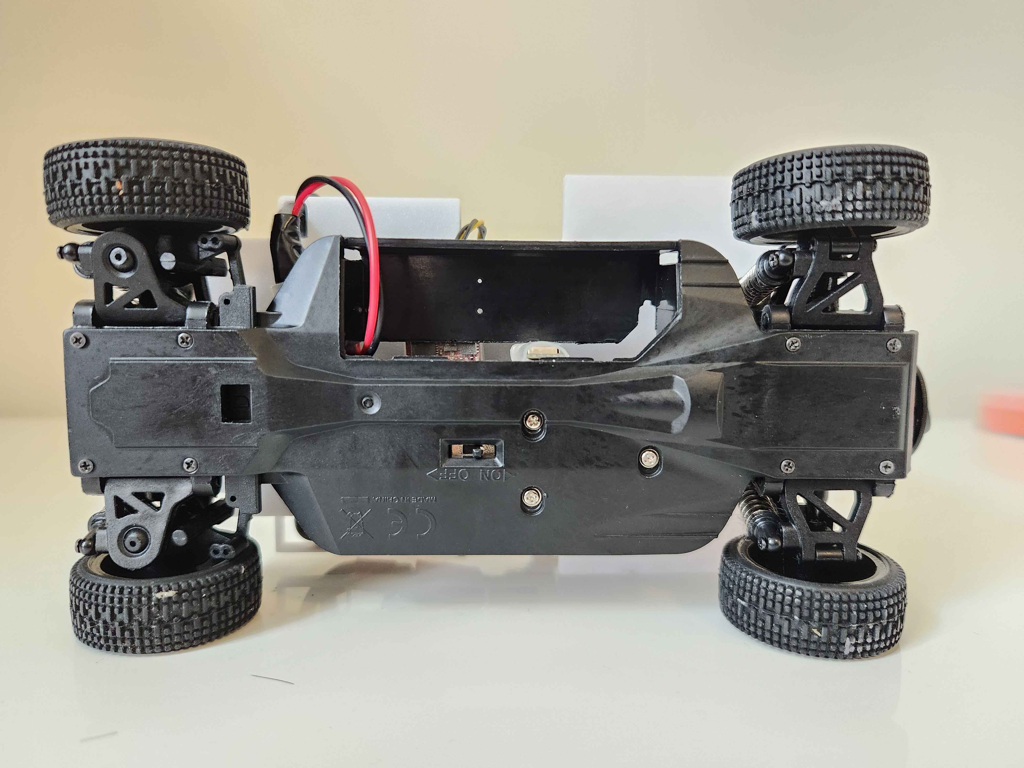
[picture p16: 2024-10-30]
v-photos/Car_Bottom_International.jpg

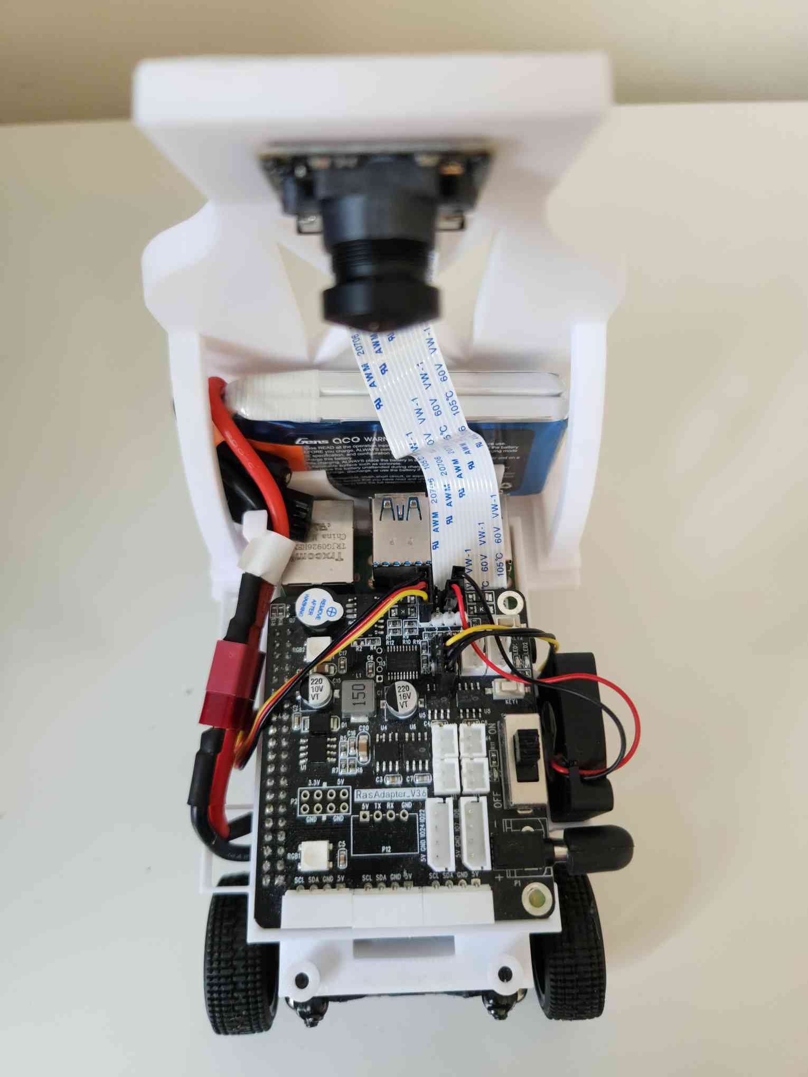
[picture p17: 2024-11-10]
v-photos/Car_Top_International.jpg

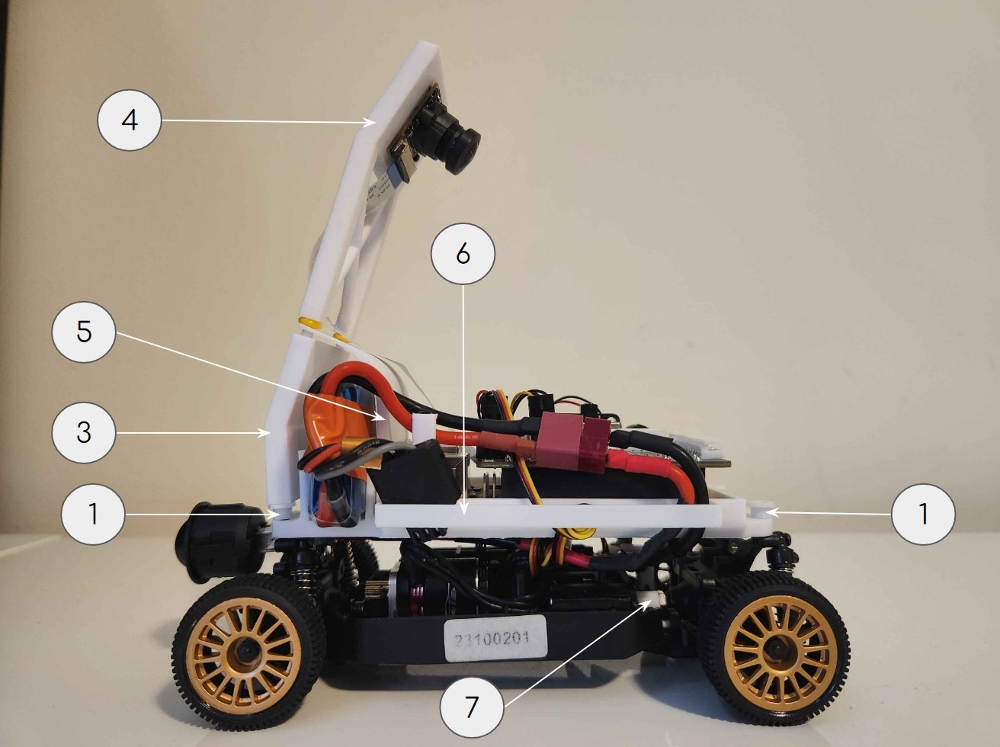
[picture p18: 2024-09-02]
other/extra images/Labeled.jpg

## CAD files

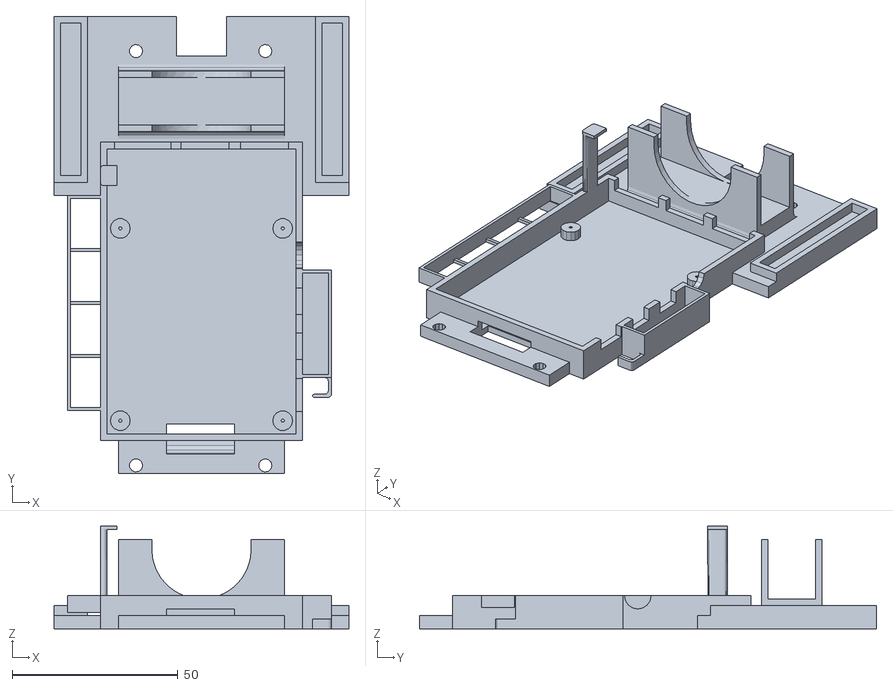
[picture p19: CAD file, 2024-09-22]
models/Car_Base_V2.stl
89.0 x 138.0 x 31.0

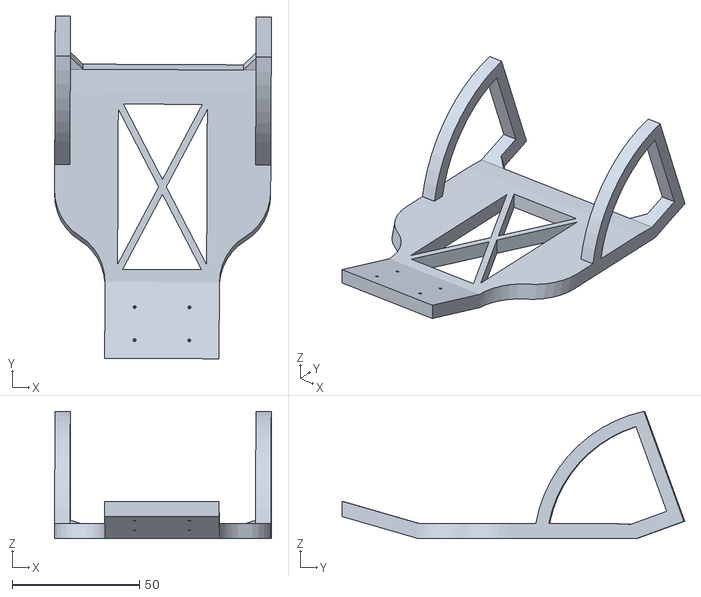
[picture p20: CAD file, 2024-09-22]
models/Camera_Mount_V2.stl
85.3 x 134.7 x 50.1

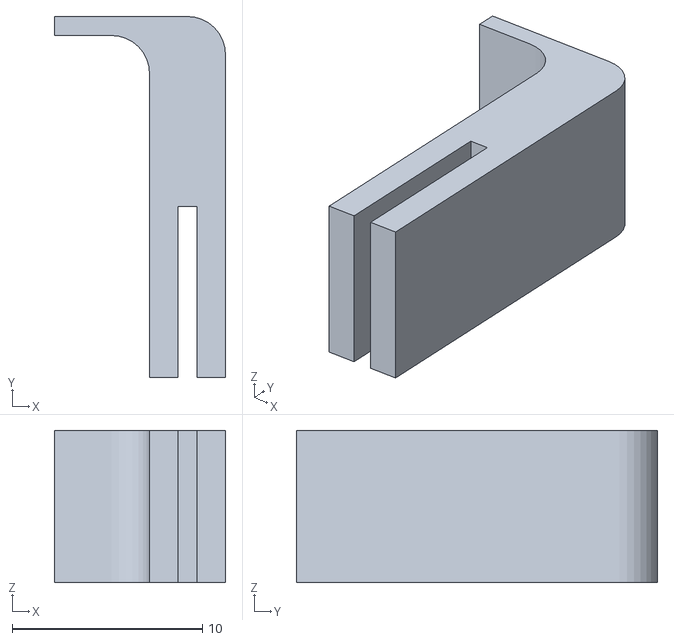
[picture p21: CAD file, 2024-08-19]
models/Cable_Barrier.stl
9.00 x 19.0 x 8.00

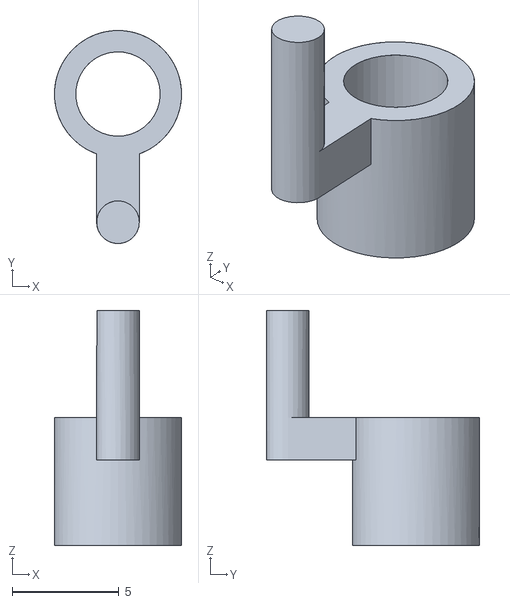
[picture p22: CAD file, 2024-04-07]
models/Servo_Attachment.stl
5.95 x 9.97 x 11.0

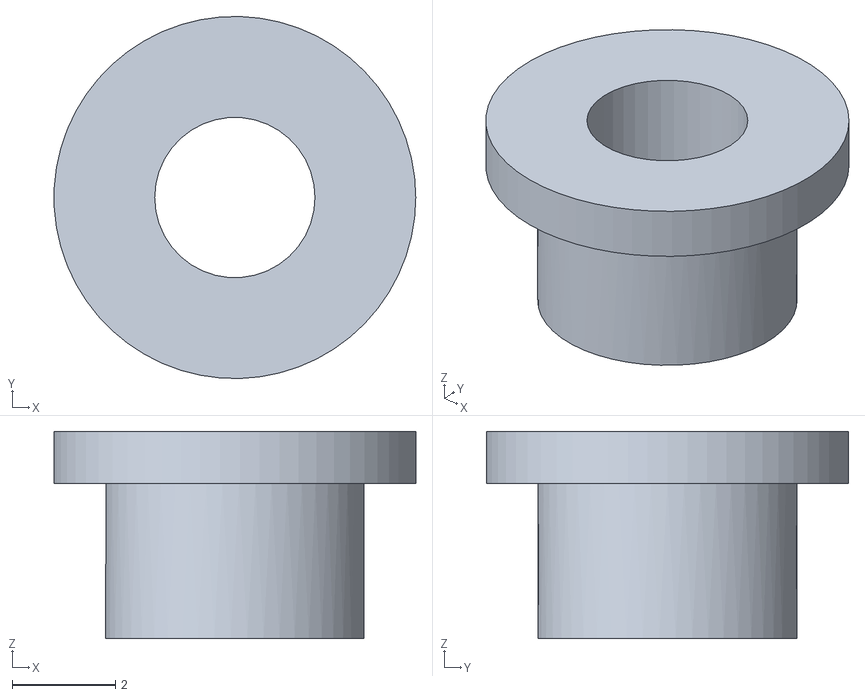
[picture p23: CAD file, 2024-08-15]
models/Base_Nut_Rear.stl
6.99 x 7.00 x 4.00

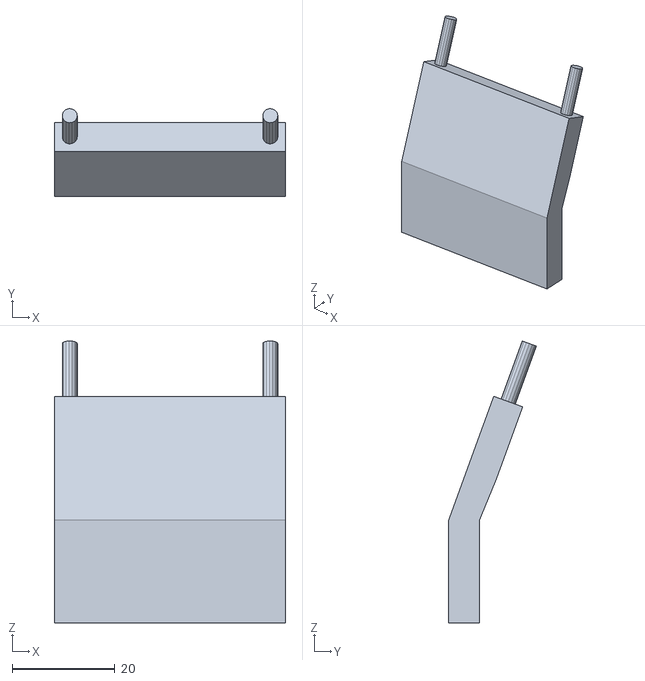
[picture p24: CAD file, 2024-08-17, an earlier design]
models/Old/Camera_Extension.stl
45.0 x 17.1 x 54.8

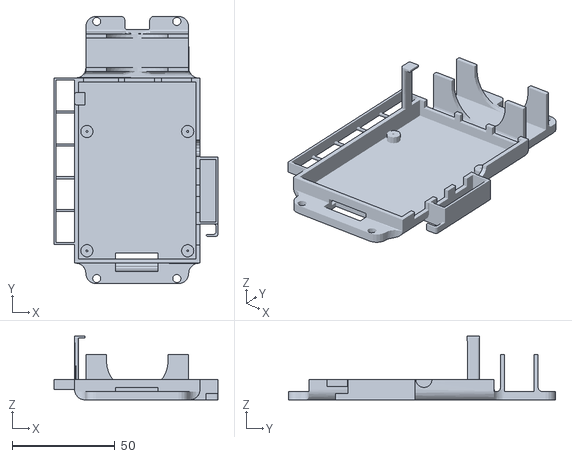
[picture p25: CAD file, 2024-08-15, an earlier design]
models/Old/Car_Base.stl
79.8 x 130.0 x 31.0

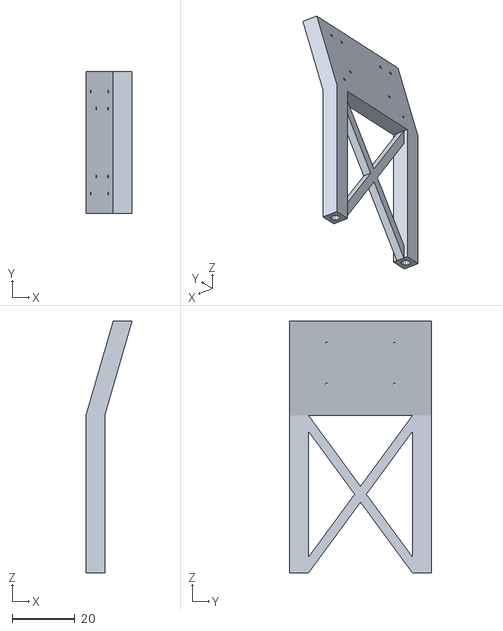
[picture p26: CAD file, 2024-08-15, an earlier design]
models/Old/Camera_Mount.stl
14.7 x 45.0 x 80.0

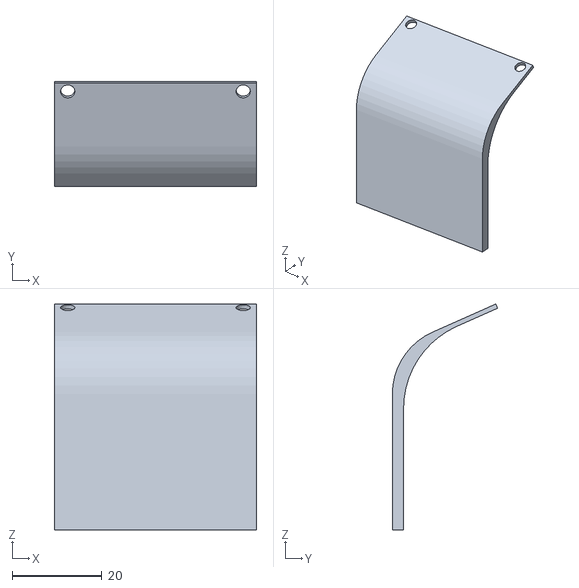
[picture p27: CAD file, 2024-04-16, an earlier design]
models/Old/Camera_Support.stl
45.0 x 23.4 x 50.2

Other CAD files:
models/Base_Nut_Front.stl

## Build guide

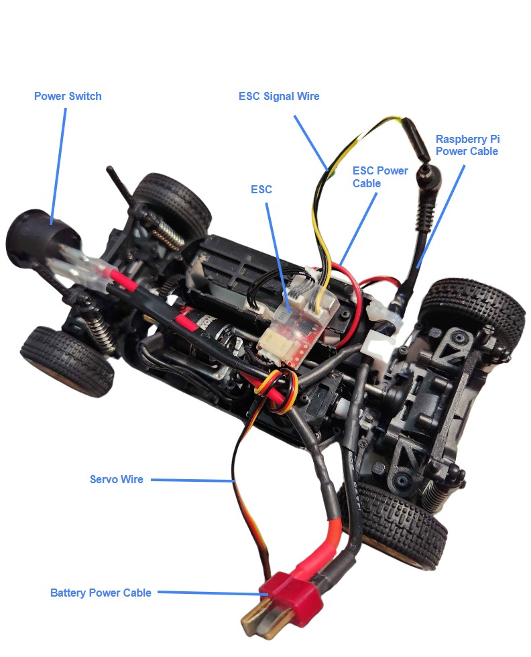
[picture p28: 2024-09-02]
other/extra images/wiring.jpg

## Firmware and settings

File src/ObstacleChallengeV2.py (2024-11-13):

# ------------------------------------------------------------{ libraries }-------------------------------------------------------------------------

import cv2
import sys
sys.path.append('/home/pi/TurboPi/')
from picamera2 import Picamera2
import libcamera
import time
import RPi.GPIO as GPIO
import numpy as np
import HiwonderSDK.Board as Board
import math
from masks import rMagenta, rRed, rGreen, rBlue, rOrange, rBlack, lotType
from functions import *

# ------------------------------------------------------------{ function / class declarations }-------------------------------------------------------------------------

class Pillar:
    def __init__(self, area, dist, x, y, target): 
        self.area = area #pillar area
        self.dist = dist #pillar distance from bottom middle point of screen
        self.x = x #pillar x
        self.y = y #pillar y
        self.target = target #stores either target of green pillars or target of red pillarss
        self.w = 0
        self.h = 0
    
    def setDimentions(self, w, h):
        self.w = w
        self.h = h

#takes in contours, selects a pillar and returns its information in the format of a Pillar object
def find_pillar(contours, target, p, colour): 
    
    global t, s, reverse, leftArea, rightArea, turnDir, maxDist
    num_p = 0
    
    for cnt in contours: 
    
        area = cv2.contourArea(cnt)
        
        #if areas are large enough for the specific colour pillar
        if (area > 150 and colour == "red") or (area > 100 and colour == "red" and tempParking) or (area > 200 and colour == "green"):
            
            #if in the time when finding the parking lot ignore green pillars with an area below 300
            if (tempParking and colour == "green" and area < 300):
                continue
            
            #get width, height, and x and y coordinates by bounding rect
            approx=cv2.approxPolyDP(cnt, 0.01*cv2.arcLength(cnt,True),True)
            x,y,w,h=cv2.boundingRect(approx)

            #since the x and y coordinates are the coordinates just in the ROI, add to the x and y values to make it the proper coordinates on the overall image
            x += ROI3[0] + w // 2 
            y += ROI3[1] + h
            
            #calculates the distance between the pillar and the bottom middle of the screen
            temp_dist = round(math.dist([x, y], [320, 480]), 0)

            #if the pillar is close enough add it to the number of pillars
            if 160 < temp_dist < 380: #180, 390
                num_p += 1
            
            #if the pillar is too close, stop the car and reverse to give it enough space
            if ((area > 6500 and target == redTarget) or (area > 8000 and target == greenTarget)) and ((x <= 420 and target == greenTarget) or (x >= 220 and target == redTarget)) and not tempParking and speed != 1500: #420, 220, 370, 270, 6500
                LED2(255, 255, 0)
                
                #move back 
                multi_write([straightConst, 0.1, 1500, 0.1, reverseSpeed, 0.5, speed])
                
                if tempParking:
                    write(1650)
                
                #if car is supposed to stop increase the timer as we moved back
                if s != 0:
                    s += 1.5
                
                #in the case of the car turning for a three point turn and seeing a pillar first instead of the wall, complete it as we have already switched directions
                if reverse == "turning" and turnDir == "right":
                    reverse = "done"
                    turnDir = "left"
                    t += 1
                
            else:
                LED2(0, 0, 0)
            
            #skips current pillar and moves on to the next if it comes too close to bottom of the screen
            if y > ROI3[3] - endConst or (target == greenTarget and (leftArea > 12000 or rightArea > 12000 or temp_dist > maxDist)) or (target == redTarget and (leftArea > 11500 or rightArea > 11500 or temp_dist > maxDist)): #370, 12500
                continue
                
            #if this pillar is closer than the current pillar replace the current pillar and update its information
            if temp_dist < p.dist:
                p.area = area
                p.dist = temp_dist
                p.y = y
                p.x = x
                p.target = target
                p.setDimentions(w, h)

    return p, num_p

if __name__ == '__main__':
    
# ------------------------------------------------------------{ initialization of variables }-------------------------------------------------------------------------
    
    time.sleep(3)
    
    #initialize camera
    picam2 = Picamera2()
    
    picam2.preview_configuration.main.size = (640,480)
    picam2.set_controls({"AeEnable": True})
    picam2.preview_configuration.main.format = "RGB888"
    picam2.preview_configuration.controls.FrameRate = 30
    picam2.preview_configuration.align()
    picam2.configure("preview")
    
    picam2.start()
    
    #stores whether a turn was counted by seeing a wall or a pillar
    eTurnMethod = ""
    
    #boolean used to indicate whether the car has stopped after 3 laps
    lapsComplete = False

    #set the target x coordinates for each red and green pillar
    redTarget = 110 
    greenTarget = 530

    #variable that keeps track of the target of the last pillar the car has passed
    lastTarget = 0

    #boolean that is used for when the car has to turn around to the opposite direction so the car can complete the last lap the other way around
    reverse = False

    #boolean storing the only direction the car is turning during the run
    turnDir = "none" 
    
    #variables to indicate when the car should park and whether it parks on the right or left side
    parkingR = False
    parkingL = False
    
    #stores a stop time 
    sTime = 0
    
    #determines how many number of seconds after sTime are needed to stop
    s = 0
    
    #tracks whether a pillar is in the first section right in front of the car, used in three-point turn determination
    pillarAtStart = -1

    #makes sure the car begins to park when no pillar is detected
    tempParking = False
    
    #determines the offset from the bottom of the ROI when the car should stop seeing a pillar
    endConst = 30
    
    #regions of interest
    #ROI1: for finding left lane
    #ROI2: for finding right lane
    #ROI3: for finding signal pillars
    #ROI4: for detecting blue and orange lines on mat
    #ROI5: helps with turns at corners
    # order: x1, y1, x2, y2
    ROI1 = [0, 175, 330, 265] # 165, 255
    ROI2 = [330, 175, 640, 265]
    ROI3 = [redTarget - 50, 120, greenTarget + 50, 345] #+- 40 [redTarget - 40, 110, greenTarget + 40, 335]
    ROI4 = [200, 260, 440, 310] #250, 300
    ROI5 = [0, 0, 0, 0] #270, 120, 370, 140
    
    ROIs = [ROI1, ROI2, ROI3, ROI4, ROI5]
    
    #booleans for tracking whether car is in a left or right turn
    lTurn = False
    rTurn = False
  
    kp = 0.015 #proportional value for PD steering 0.015
    kd = 0.01 #derivative value for PD steering 0.01

    cKp = 0.2 #value of proportional for proportional steering for avoiding signal pillars
    cKd = 0.2 #value of derivative for proportional and derivative sterring for avoiding signal pillars
    cy = 0.15 #value used to affect pd steering based on how close the pillar is based on its y coordinate
  
    straightConst = 87 #angle in which car goes straight
    exitThresh = 4000 #if area of both lanes is over this threshold car exits a turn
  
    angle = 87 #variable for the current angle of the car
    prevAngle = angle #variable tracking the angle of the previous iteration
    tDeviation = 50 #value used to calculate the how far left and right the car turns during a turn, could actually be 50
    sharpRight = straightConst - tDeviation #the default angle sent to the car during a right turn
    sharpLeft = straightConst + tDeviation #the default angle sent to the car during a left turn
    
    speed = 1660 #variable for initial speed of the car
    reverseSpeed = 1340 #variable for speed of the car going backwards
    
    aDiff = 0 #value storing the difference of area between contours
    prevDiff = 0 #value storing the previous difference of contours for derivative steering

    error = 0 #value containing the difference between a pillar's x coordinate and its target x coordinate
    prevError = 0 #stores previous error
    
    maxDist = 370 #no pillar can be detected if further than this value
    
    t = 0 #tracks number of turns
    t2 = 0 #tracks number of turns but updates only when seeing a coloured line at a corner
    
    tSignal = False #boolean detecting whether a coloured line is currently seen, makes sure that a pillar doesn't affect a turn too early
    
    LED1(255, 0, 0)
    
    write(1500) # send initial value to esc for calibration

    time.sleep(8) #delay 8 seconds for the servo to be ready
    
    debug = False #boolean for debug mode
   
    #code for starting button
    key2_pin = 16
    
    GPIO.setmode(GPIO.BOARD)
    GPIO.setup(key2_pin, GPIO.IN, pull_up_down = GPIO.PUD_UP)
    
    LED1(0, 255, 0)
    
    #set mode based on program arguments
    if len(sys.argv) > 1:
        debug = True
        
        if sys.argv[1].lower() == "parkingl": #for testing parking on the left side
            t = 12
            turnDir = "right"
            ROI3[1] = 140
            speed = 1650
        elif sys.argv[1].lower() == "parkingr": #for testing parking on the left side
            t = 12
            turnDir = "left"
            ROI3[1] = 140
            speed = 1650
        elif sys.argv[1].lower() == "psteer": #for testing parking on the left side
            tempParking = True
            t = 12
            t2 = 12
            speed = 1500
        elif sys.argv[1].lower() == "stop": #for testing parking on the left side
            t = 11
        elif sys.argv[1].lower() == "turnt": #for testing three-point turns (pillar in front)
            t = 7
            speed = 1660
            pillarAtStart = True
        elif sys.argv[1].lower() == "turnf": #for testing three-point turns (no pillar in front)
            t = 7
            speed = 1660
            pillarAtStart = False
        elif sys.argv[1].lower() == "steer": #for stationary testing
            speed = 1500
        elif sys.argv[1].lower() == "fast": #for stationary testing
            speed = 1660
        
        
    #if no mode is specified, assume the regular program and wait for button input
    else:
        buzz()
        while GPIO.input(key2_pin) == GPIO.HIGH:
            pass
        
        time.sleep(2)
        
    LED1(0, 0, 0)
    
    #used to track time elapsed
    pTimer = time.time()
    
    start = False
    
    #used to determine whether there is a pillar directly in front of the car
    startArea = 0
    startTarget = 0

# ------------------------------------------------------------{ main loop }-------------------------------------------------------------------------
    while True:
        
        #used in fps calculation
        fps_start = time.time()

# ------------------------------------------------------------{ contour detection of walls, pillars, and orange and blue lines }-------------------------------------------------------------------------
        
        #stop the car after the third lap
        if sTime != 0 and not lapsComplete:
            if time.time() - sTime > s:
                multi_write([1500, 5, 1680, 0.1, 1650])
                lapsComplete = True
                
        #reset rightArea, and leftArea variables
        rightArea, leftArea, areaFront, areaFrontMagenta, tArea = 0, 0, 0, 0, 0

        #get an image from pi camera
        img = picam2.capture_array()
        
        # convert from BGR to HSV
        img_lab = cv2.cvtColor(img, cv2.COLOR_BGR2Lab)
        
        #perform Gaussian Blur
        img_lab = cv2.GaussianBlur(img_lab, (7, 7), 0)
        
        #find area of right parking lot to help with avoiding it
        if not tempParking:
            pRight = find_contours(img_lab, rMagenta, ROI2)
            rPArea = max_contour(pRight, ROI2)[0]

        #find area of ROI5 to make sharper turns at corners
        if ROI5[0] != 0: 
            contours_turn = find_contours(img_lab, rBlack, ROI5)
            contours_turn_m = find_contours(img_lab, rMagenta, ROI5)
            tArea = max_contour(contours_turn, ROI5)[0] + max_contour(contours_turn_m, ROI5)[0]

        #get contours of left and right walls
        if tempParking:
            contours_left = pOverlap(img_lab, ROI1)
            contours_right = pOverlap(img_lab, ROI2)
        else:
            contours_left = pOverlap(img_lab, ROI1, True)
            contours_right = pOverlap(img_lab, ROI2, True)

        #find areas of left and right walls
        leftArea = max_contour(contours_left, ROI1)[0]
        rightArea = max_contour(contours_right, ROI2)[0]

        #find area of black in front of car, used in three point turn and parking
        contours_parking = find_contours(img_lab, rBlack, ROI4)
        areaFront = max_contour(contours_parking, ROI4)[0]
        
        #find contours of pillars
        contours_red = find_contours(img_lab, rRed, ROI3)
        contours_green = find_contours(img_lab, rGreen, ROI3)

        #find contours of orange and blue lines
        contours_blue = find_contours(img_lab, rBlue, ROI4)
        contours_orange = find_contours(img_lab, rOrange, ROI4)
        
# ------------------------------------------------------------{ processing contours }-------------------------------------------------------------------------
        
        #count number of red and green pillars
        num_pillars_g = 0
        num_pillars_r = 0

# -----------------{ green / red signal pillar contour processing }--------------

        #make a temporary pillar object
        temp = Pillar(0, 1000000, 0, 0, greenTarget)

        #find pillar to navigate around
        cPillar, num_pillars_g = find_pillar(contours_green, greenTarget, temp, "green")
        cPillar, num_pillars_r = find_pillar(contours_red, redTarget, cPillar, "red")
        
        #before first turn update the largest area found to determine if there was a pillar directly in front of the car
        if t == 0:
            if cPillar.area > startArea:
                startArea = cPillar.area
                startTarget = cPillar.target
        
        #draw contours of pillars for debugging
        if debug: cv2.drawContours(img[ROI3[1]:ROI3[3], ROI3[0]:ROI3[2]], contours_green, -1, (144, 238, 144), 2)
        if debug: cv2.drawContours(img[ROI3[1]:ROI3[3], ROI3[0]:ROI3[2]], contours_red, -1, (144, 144, 238), 2)
                
# -----------------{ control variable manipulation based on number of pillars }--------------

        #lower control variables if there are more than 2 pillars of the same colour, most likely meaning we are turning along an inside corner.
        if num_pillars_g >= 2 or num_pillars_r >= 2:
            
            LED2(255, 255, 255)
        
            endConst = 70 #60
            
            cKp = 0.2 
            cKd = 0.2 
            cy = 0.05
    
        #any other combination of number of pillars
        else: 
            
            LED2(0, 0, 0)     
            
            endConst = 40 #30
            
            if tempParking:
                endConst = 30
            
            cKp = 0.25 #0.25
            cKd = 0.25 #0.25
            cy = 0.08 #0.08

# -----------------{ orange / blue line contour processing }---------------

        #find the areas of blue and orange lines
        maxO = max_contour(contours_orange, ROI3)[0]
        maxB = max_contour(contours_blue, ROI3)[0]

        #set a turn direction if this is the first turn
        if turnDir == "none":
            if maxO > 100: 
                turnDir = "right"
            elif maxB > 100: 
                turnDir = "left"
        
        #if corresponding coloured line is detected (orange for right turns, blue for left turns)
        if (turnDir == "right" and maxO > 100) or (turnDir == "left" and maxB > 100): 
            
            #update t2
            t2 = t
            
            if t2 == 7:
                if not pillarAtStart:
                    #readjust region of interest so pillars are seen earlier
                    ROI3[1] = 110
            
            #show ROI5 to make sharper turns during the lap where parking is performed
            if tempParking:
                ROI5 = [270, 120, 370, 140]
            
            #show ROI5 when approaching a corner narrow
            if cPillar.area != 0 and ((leftArea > 500 and turnDir == "left") or (rightArea > 500 and turnDir == "right")):
                ROI5 = [270, 120, 370, 140]

            #set either the right or left turn to true based on turn direction
            if turnDir == "right":
                rTurn = True
            else:
                lTurn = True

            #determine if there was a pillar directly in front by checking the biggest pillar's area and colour (target). 
            if t == 0 and pillarAtStart == -1:
                print("start area:", startArea)
                if (startArea > 2500 and startTarget == greenTarget) or (startArea > 1500 and startTarget == redTarget): #3000, 2000
                    pillarAtStart = True
                else:
                    pillarAtStart = False
            
            #indicate that the coloured line is seen
            tSignal = True
        
        #second line after turning line is detected
        elif (turnDir == "left" and maxO > 100) or (turnDir == "right" and maxB > 100):
            #set a timer to stop at the end of the third lap
            if t2 == 11:
                s = 2

                sTime = time.time()
        
        #indicate there was a pillar right after start if there have been 2 red or green pillars detected
        if pillarAtStart == -1 and (num_pillars_g >= 2 or num_pillars_r >= 2): 
            pillarAtStart = True
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

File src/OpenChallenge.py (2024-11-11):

#import necessary libraries
import sys
sys.path.append('/home/pi/TurboPi/')
import cv2
from picamera2 import Picamera2
from time import sleep
import RPi.GPIO as GPIO
import numpy as np
import threading
import HiwonderSDK.Board as Board
import time
from functions import *
from masks import rOrange, rBlack, rBlue
    
if __name__ == '__main__':
    
    time.sleep(3)

    #initialize camera
    picam2 = Picamera2()
    picam2.preview_configuration.main.size =(640,480)
    picam2.preview_configuration.main.format = "RGB888"
    picam2.preview_configuration.controls.FrameRate = 30
    picam2.preview_configuration.align()
    picam2.configure("preview")
    picam2.start()

    #lists storing coordinates for the regions of interest to find contours of the lanes and the orange line 
    # order: x1, y1, x2, y2
    ROI1 = [20, 170, 240, 220]
    ROI2 = [400, 170, 620, 220] # 380, 600 | 400, 620
    ROI3 = [200, 300, 440, 350]

    #booleans for tracking whether car is in a left or right turn
    lTurn = False
    rTurn = False
  
    t = 0 #number of turns car has completed
    
    kp = 0.02 #value of proportional for proportional steering
    kd = 0.006 #value of derivative for proportional and derivative sterring
    
    straightConst = 87 #angle in which car goes straight

    turnThresh = 150 #if area of a lane is under this threshold car goes into a turn
    exitThresh = 1500 #if area of both lanes is over this threshold car exits a turn
  
    angle = 87 #variable for the current angle of the car
    prevAngle = angle #variable tracking the angle of the previous iteration
    tDeviation = 25 #value used to calculate the how far left and right the car turns during a turn
    sharpRight = straightConst - tDeviation #the default angle sent to the car during a right turn
    sharpLeft = straightConst + tDeviation #the default angle sent to the car during a left turn
    
    #maximum limit for angles
    maxRight = straightConst - 50
    maxLeft = straightConst + 50
    
    speed = 1665 #variable for the speed of the car, 1665
    
    aDiff = 0 #value storing the difference of area between contours
    prevDiff = 0 #value storing the previous difference of contours for derivative steering
    
    write(1500)
    LED1(255, 0, 0)

    sleep(8) #delay 8 seconds for the servo to be ready

    #boolean tracking whether the orange line on the mat is detected
    lDetected = False
    
    #boolean tracking whether we are in debug mode or not 
    debug = False
    
    #set up button 
    key2_pin = 16
    
    GPIO.setmode(GPIO.BOARD)
    GPIO.setup(key2_pin, GPIO.IN, pull_up_down = GPIO.PUD_UP)
    
    LED1(0, 255, 0)
    
    #change debugging mode based on program arguments
    if len(sys.argv) > 1 and sys.argv[1] == "Debug":
        debug = True
    else:
        buzz()
        #wait until button press
        while GPIO.input(key2_pin) == GPIO.HIGH:
            pass
        
        time.sleep(3)
        
    LED1(0, 0, 0)
    LED2(0, 0, 255)
    
    start = False
    turnDir = "none"

    #main loop
    while True:
          
        #declare variables for the areas of the left and right contours
        rightArea, leftArea = 0, 0

        #get an image from pi camera
        img = picam2.capture_array()
        
        # convert from BGR to LAB
        img_lab = cv2.cvtColor(img, cv2.COLOR_BGR2Lab)
        
        #blur image
        img_lab = cv2.GaussianBlur(img_lab, (7, 7), 0)
        
        #find contours of walls and orange and blue lines
        cListLeft = find_contours(img_lab, rBlack, ROI1)
        cListRight = find_contours(img_lab, rBlack, ROI2)
        cListOrange = find_contours(img_lab, rOrange, ROI3)
        cListBlue = find_contours(img_lab, rBlue, ROI3)
        
        #find areas of walls
        leftArea = max_contour(cListLeft, ROI1)[0]
        rightArea = max_contour(cListRight, ROI2)[0]
        
        #indicate if orange line or blue line is detected and set turn direction accordingly
        if max_contour(cListOrange, ROI3)[0] > 100: 
            lDetected = True
            if turnDir == "none":
                turnDir = "right"
        elif max_contour(cListBlue, ROI3)[0] > 100:
            lDeteted = True
            if turnDir == "none":
                turnDir = "left"
        
        #draw contours
        cv2.drawContours(img[ROI3[1]:ROI3[3], ROI3[0]:ROI3[2]], cListOrange, -1, (0, 255, 0), 2)
        cv2.drawContours(img[ROI1[1]:ROI1[3], ROI1[0]:ROI1[2]], cListLeft, -1, (0, 255, 0), 2)
        cv2.drawContours(img[ROI2[1]:ROI2[3], ROI2[0]:ROI2[2]], cListRight, -1, (0, 255, 0), 2)
        
        #calculate difference of areas between the areas of the lanes
        aDiff = rightArea - leftArea

        #calculate angle using PD steering
        angle = int(max(straightConst + aDiff * kp + (aDiff - prevDiff) * kd, 0)) 

        #if the area of either lane is less than or equal to turnThresh and the car is not in a turn going the other direction, set the boolean of the respective direction turn to true
        if leftArea <= turnThresh and not rTurn:

            lTurn = True
            LED1(255, 0, 0)

        elif rightArea <= turnThresh and not lTurn:

            rTurn = True
            LED1(255, 0, 0)
            
        if not start:
            #write intial values to car
            multi_write([2, angle, 0.5, speed])
            start = True

        #if angle is different from previous angle
        if angle != prevAngle:
            #if car is in a left or right turn
            if lTurn or rTurn: 

              #if the area of the lane the car is turning towards is greater than or equal to exitThresh, the turn is completed and the booleans are set to false and the number of turns is increased by 1
              if (rightArea > exitThresh and rTurn) or (leftArea > exitThresh and lTurn): 
                  #set turn variables to false as turn is over
                  lTurn = False 
                  rTurn = False
                  
                  LED1(0, 255, 0)

                  #reset prevDiff
                  prevDiff = 0 
                  
                  #increase number of turns by 1 only if the orange line has been detected 
                  if lDetected: 
                      t += 1

                      if t == 4:
                          LED2(255, 255, 0)
                      elif t == 8:
                          LED2(255, 255, 255)
                        
                      lDetected = False

              #set the angle to the default angle for turns if in a turn, 
              #if the calculated angle is sharper than the default angle and is within the limits of maxLeft and maxRight, use that angle instead
              elif lTurn:
                  angle = min(max(angle, sharpLeft), maxLeft)
              elif rTurn: 
                  angle = max(min(angle, sharpRight), maxRight)
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

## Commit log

2024-04-01 Update README.md
    Change made to motor + esc link
2024-04-07 added servo attachment stl
    [Servo_Attachment.stl]
2024-04-08 updated base with a battery holder
    [Car_Base.stl]
2024-04-09 added camera extension
    [Camera_Extension.stl]
2024-04-10 added additional camera extension
    [Camera_Extension_Top.stl]
2024-04-30 added debug mode, button to start, leds, and buzzer
    [OpenChallenge.py]
2024-05-01 turned off leds after done laps
2024-05-04 added a three point turn to switch directions after second lap
2024-05-28 fixed error where it calculates distance with contour dimensions instead of screen dimensions
    [ObstacleChallenge.py]
2024-06-08 fixed three point turn and fixed 2 pillar inner corner cases
    [ObstacleChallenge.py]
2024-06-08 removed merging conflicts, previous commit was reworking three point turn and fixing 2 pillar inner corner cases
    [ObstacleChallenge.py]
2024-06-23 Update README.md
    On-Off Switch added to table of components
2024-06-23 car now moves back if too close to pillar to readjust
    [ObstacleChallenge.py]
2024-06-29 reworked the three point turn to disregard a pillar in the center of a straight section
    [ObstacleChallenge.py]
2024-07-01 added files for gyro sensor usage
2024-07-01 imported libraries to be able to get heading values from gyro
2024-07-01 added calibration values and fixed errors
2024-07-01 added logic to follow a specific heading using the gyro sensor
2024-07-03 added turning into parking lot and made it run laps following gyro headings
2024-07-19 changed calibration values
2024-07-24 updated camera mount to hold gyro and organize wires
    [Camera_Mount.stl]
2024-07-25 changed gyro calibration values
2024-07-28 added file used for getting gyro values for each direction
2024-07-28 fixed error and updated gyro values
    [ObstacleChallenge.py]
2024-07-30 updated gyro usage and switched to heading over compensated heading
2024-08-05 severely changed parking algorithm to no longer use gyro
    [ObstacleChallenge.py]
2024-08-08 added extensions for cable management
    [Car_Base.stl]
2024-08-11 Updated Components List
    Removed the IMU sensor, as after a month of testing, the one originally acquired was found to give inconsistent readings
2024-08-15 fixed orientation
    [Camera_Mount.stl]
2024-08-17 combined both extension pieces
    [Camera_Extension.stl]
2024-08-17 ensures no interference between wires and wheels
    [Cable_Barrier.stl]
2024-08-19 made barrier larger and added ledge to catch wire
    [Cable_Barrier.stl]
2024-08-19 increased thickness and changed width and length
    [Cable_Barrier.stl]
2024-08-22 added a u turn failsafe for parking and a way to ignore objects outside of the track
    [ObstacleChallenge.py]
2024-08-23 adjusted timings and control variables for avoiding signal pillars
    [ObstacleChallenge.py]
2024-08-24 fixed small issues in specific cases in three point turn and parking
    [ObstacleChallenge.py]
2024-08-27 added pause after 3 laps and fixed bug with 3 point turn
    [ObstacleChallenge.py]
2024-08-30 small changes to fix issues with three point turn and parking
    [ObstacleChallenge.py]
2024-09-01 Added team photos and electricity and power information
2024-09-01 updated motor section
2024-09-01 highlighted key terms in motor section
2024-09-01 updated description in motor section
2024-09-01 added overview of 3D-printed components
2024-09-01 added schematic
2024-09-01 Edited camera vision section
2024-09-01 added wiring diagram
2024-09-02 removed need for noPillar variable and fixed issue with specific case in three-point turn
    [ObstacleChallenge.py]
2024-09-02 added updated wiring diagram
2024-09-22 added folder for old models not used anymore
    [Camera_Extension.stl, Camera_Mount.stl, Camera_Support.stl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]
2024-09-22 added updated camera mount that is one piece
    [Camera_Mount_V2.stl]
2024-09-22 updated car base to accomodate new camera mount
    [Car_Base_V2.stl]
2024-09-26 fixed small bug with turns
    [ObstacleChallengeV2.py]
2024-10-28 general small changes to obstacle avoidance and parking
    [ObstacleChallengeV2.py]
2024-10-30 Elaborated on existing, unchanged elements of our car
    Edited Mobility and Sensors sections
2024-10-31 updated chassis section with a possible improvement
2024-11-01 added possible chassis modification for improvements
2024-11-09 updated assembly instructions
2024-11-09 added raspberry pi OS file link
2024-11-09 added possible gyro improvement
2024-11-09 updated aspects of motors and power management
2024-11-09 updated chassis section
2024-11-10 updated heading sizes in mobility management + power and sense management
2024-11-11 Update Power and Sense Management sections
2024-11-11 added information about camera
2024-11-11 updated information about servo motor
2024-11-11 Updated servo section
2024-11-11 now dc motor starts after first angle is calculated
2024-11-11 changed when motor is started, now blue line is also used, and stop delay changes based on turn direction
